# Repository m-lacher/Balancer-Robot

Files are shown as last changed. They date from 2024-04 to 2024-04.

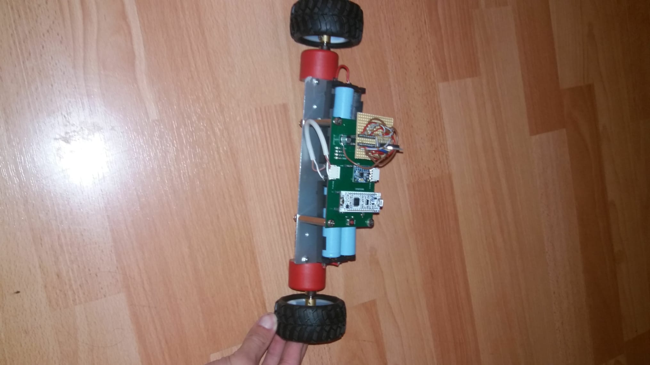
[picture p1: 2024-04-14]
Documentation/Bilder/b0cf12ee-8584-46d6-8bd2-6b98735de912.jpg

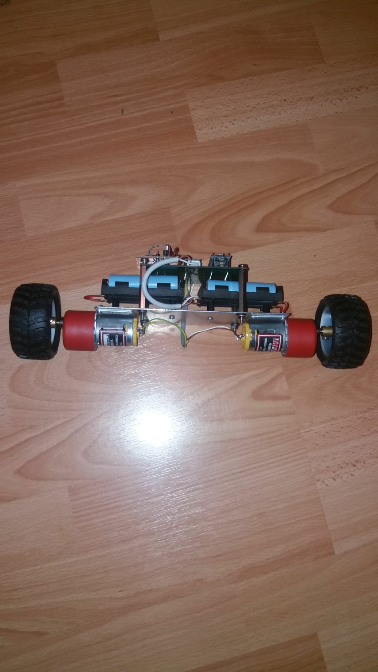
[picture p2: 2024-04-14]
Documentation/Bilder/f380182b-9d1d-40e0-8857-80b62b0fd65c.jpg

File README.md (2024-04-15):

# Balancer-Robot
## Introduction
The Balancer Robot was my project for the "Berufsmaturitätsarbeit" (BMA). The goal of this project was to design a self-balancing two wheeled robot. 
## Note
The project was quite a bit of a challenge, as I hadn't had much knowledge about control systems or desinging the mechanical system. However after many tries, the robot balanced itself quite good. This can be seen in the [BalancerRobot.mp4](/Balancer%20Robot.mp4) video.

## Further documentation
Further information can be found in the [Documentation](/Documentation/) folder.\
Project documentation: [BMA-BalancerRobot.pdf](/Documentation/BMA-BalancerRobot.pdf)

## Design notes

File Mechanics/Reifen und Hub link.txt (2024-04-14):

Reifen:	https://www.play-zone.ch/de/wheel-72x34mm-blau.html

Hub:	https://www.play-zone.ch/de/wheel-hub.html

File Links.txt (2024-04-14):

batterie holder:	https://www.digikey.ch/product-detail/de/keystone-electronics/1047/36-1047-ND/5057794?productid=5057794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

i2c problem:		https://os.mbed.com/questions/84778/I2C-doesn-t-work-on-F303K8/
			https://www.mikrocontroller.net/topic/454653

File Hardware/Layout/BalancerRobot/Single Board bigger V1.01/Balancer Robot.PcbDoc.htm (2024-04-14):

Reporting Options

# File in Previous Format

Date | : | 22.03.2023
Time | : | 16:07:12
Filename | : | C:\Backup HDD\BalancerRobot\Hardware\Layout\BalancerRobot\Single Board bigger V1.01\Balancer Robot.PcbDoc

Version | Warning

This file was generated by an earlier version of the software

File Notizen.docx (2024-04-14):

15.09.2019: PWM programmiert, erster Versuch

17.09.2019: Ansteuerung Sensor erfolgreich.

19.09.2019: Layout bestellt.

19.09.2019: Testversuche mit Sensor

23.09.2019: Weitere Testversuche, Auswertung.

30.09.2019: Mechanische Grundplatte bei Andreas in Auftrag gegeben.

03.10.2019: Erste Version zusammengebaut.

04.10.2019: Bemerkt, dass Pullup Widerstände fehlen. Neuer Sensor bestellt

08.10.2019: Diskussion mit Volker über die physikalischen Kräfte sowie eine Reglung durch Impulsansteuerung der Motoren. (Pendelprinzip)

15.10.2019: Problem mit Umzug (Mechanische und elektronische Fertig erschwert)

17.10.2019: Problem mit I2C festgestellt.

21.10.2019: Mikrocontroller ausgelötet wegen Widerstandsbrücken, am Abend festgestellt, dass Mikrocontroller kaputt ist.

22.10.2019: Mikrocontroller ausgelötet, Leiterplatte kaputt. Neue Bauteile bestellt.

23.10.2019: An Doku gearbeitet, am Nachmittag im Geschäft um neue Leiterplatte zu bestücken, Motoren getest, festgestellt dass IC zu heiss. IC getauscht, Kurzschluss, Mikrocontroller und IC kaputt.

24.10.2019: Software überarbeitet, test ohne Motoren gelungen, Nachmittag neue Motor Treiber in Nänikon abgeholt.

25.10.2019: Neuer Motortreiber auf Adapterplatte gelötet, Ansteuerung funktionierte, später dann jedoch bei einem Motor nicht Rückwärts.

28.10.2019: Viel an der Dokumentation gearbeitet.

30.10.2019: Festgestellt, dass ein Wackelkontakt bei der Adapterplatine vorhanden ist, weshalb der Motor nicht drehte.

31.10.2019: Entschieden ein neues Layout zu erstellen.

04.11.2019: Layout angepasst

05.11.2019: Layout online bestellt.

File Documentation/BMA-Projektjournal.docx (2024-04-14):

Lacher Markus, BEL16a

markuslacher@hotmail.ch

Balancer Robot

Prozessdokumentation

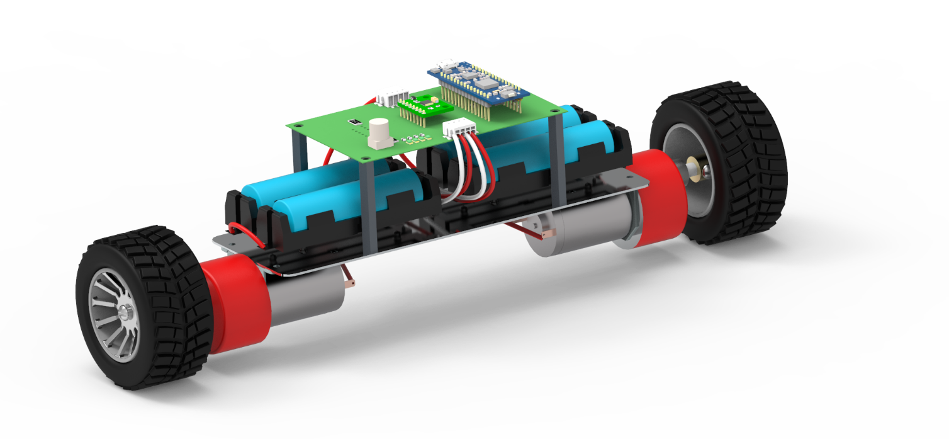
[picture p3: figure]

Berufsmaturitätsschule Zürich

Technik, Architektur, Life Sciences

Betreuer: H.P. Lutz

Abgabe: 26.11.2019

# Projektvereinbarung

## Thema

Der Balancer Robot soll ein Fahrzeug werden, welches sich selbst ausbalanciert. Es soll auf 2 Rädern vor- und zurückfahren, um nicht umzufallen. Ein grosser Teil des Projekts umfasst das Entwickeln der Elektronik und der Software des Fahrzeugs. Mithilfe eines Beschleunigungs- und Gyrosensors soll die Neigung des Fahrzeugs bestimmt werden können. Die Software soll dann per Regelungsalgorithmus die Motoren ansteuern, damit der Balancer Robot vor dem Umfallen bewahrt wird. Sowohl die Elektronik, als auch die Software bilden eine Herausforderung, der ich mich jedoch gewachsen fühle. Der Regelungsalgorithmus wird wahrscheinlich die grösste Herausforderung werden. Fokus der Arbeit ist also das Bereitstellen eines funktionstüchtigen und optimierten Prototyps. Sollte dieser funktionieren, werde ich mit ersten Selbstversuchen simpler Regelungsalgorithmen beginnen.

## Eigene Fragestellung / Untersuchungsgegenstand

### Leitfrage

Ist es möglich, mithilfe eines Beschleunigungs- und Gyrosensors und zwei DC-Motoren ein Fahrzeug auf 2 Rädern auszubalancieren? Untersucht werden soll dabei einerseits die Physik hinter dem Ausbalancieren, andererseits soll eine Elektronik entwickelt werden, die bestmöglich auf das Ausbalancieren optimiert ist. Zusätzlich möchte ich Gedanken und Recherche über Regelungsalgorithmen ausführen, um allfällig selber den Regelungsalgorithmus für das Ausbalancieren schreiben zu können.

### Hypothese

Ich denke, das Bestimmen der Neigung mithilfe des Beschleunigungs- und Gyrosensors sollte möglich sein. Auch das Entwickeln der Elektronik traue ich mir zu. Schwieriger wird es bei der Software für den Mikrocontroller. Die ist vermutlich relativ komplex. Aber da ich aktuell im Geschäft über programmieren von Embedded Software geschult werde, möchte ich mich dieser Herausforderung stellen. Die grösste Schwierigkeit sehe ich im Regelungsalgorithmus, da ich mich bis anhin weder in der Schule noch im Geschäft mit Regelungstechnik befasst habe.

### Methoden und Vorgehen

Geplant sind 4 Projektmeilensteine: Zu Beginn das Analysieren des physikalischen Grundprinzips. Danach soll die Elektronik und die Mechanik für den ersten Prototypen entwickelt werden. Im dritten Schritt soll Software entwickelt werden, um die Elektronik anzusteuern. Der vierte Meilenstein wird das Entwickeln eines Regelungsalgorithmus sein.

## Hilfsmittel

Messgeräte für das Testen der Elektronik, sowie Debugger für die Software. 3D-CAD Programm für die Mechanik.

## Kontaktpersonen, Informationsstellen, Institutionen

Eine wichtige Kontaktperson wird Herr Lutz sein, weil ich sicherlich Unterstützung beim Analysieren des physikalischen Prinzips brauche. Herr Malacarne, mein Elektrotechniklehrer aus der Berufsschule, wird meine erste Anlaufstelle sein, wenn es Probleme in der Elektronik gibt. Für den Regelungsalgorithmus könnte ich einen Projektleiter aus meinem Geschäft ansprechen, Herrn Gwerder, da dieser einen Master in Regelungstechnik besitzt.

## Persönlicher Bezug / Motivation

Das Projekt ist eine grosse Herausforderung für mich. Es wird viel Zeit in Anspruch nehmen und es ist gut möglich, dass am Ende das Ausbalancieren nicht funktioniert. Dennoch bin ich motiviert, mein Können unter Beweis zu stellen und das Beste aus dem Projekt zu machen. Ich wollte mich schon seit Längerem mit Regelungstechnik auseinandersetzen, hatte bisher aber nicht die Zeit dafür. Dieses Projekt kombiniert ideal meine Interessen im Bereich der Softwareprogrammierung, Entwicklung von Elektronik und Physik.

# Zeitplan

# Protokoll der Zwischenbesprechung

Eine offizielle Zwischenbesprechung wurde nicht durchgeführt. In der Projektwoche setzte sich Herr Lutz kurz zu mir und fragte mich nach dem Stand und den Problemen des Projekts. Er gab mir Tipps und Vorschläge und überprüfte, ob ich mich auf dem richtigen Weg befinde. Ein Protokoll wurde nicht geführt.

# Projektjournal

Datum | Ausgeführte Arbeiten | Aufwand
19.08.2019 | Erste Überlegungen zum Projekt und zu den physikalischen Kräften gemacht. | 3h
23.08.2019 | Informiert über Gyrosensoren und Beschleunigungssensoren. Sensorboard bestellt. Zwei verschiedene Motoren auf Conrad bestellt. | 2h 0.5h 0.5h
27.08.2019 | Mechanische Planung, Grobkonzept des ersten Prototyps erstellt. Mindestanforderung für das Motorendrehmoment bestimmt. | 1.5h 1h
28.08.2019 | Festgestellt, dass die bestellten Motoren ein zu kleines Drehmoment aufweisen. Motor mit mechanischer Übersetzung auf Conrad bestellt. | 1.5h
15.09.2019 | Erste Software geschrieben, um die PWM Ansteuerung des Mikrocontrollers zu testen. | 1.5h
17.09.2019 | Ansteuerung des Sensors MPU-6050 erfolgreich getestet. Schema für die Leiterplatte entwickelt. | 2h 1h
19.09.2019 | Erste Leiterplatte gelayoutet und bestellt. | 8h
23.09.2019 | Weitere Testversuche mit dem Sensor, Softwaremodul programmiert. | 2h
25.09.2019 | Python-Skript programmiert, um die Sensorwerte mit dem Computer auslesen zu können. | 1.5h
30.09.2019 | Mechanische Grundplatte gezeichnet und einem Mechaniker im Betrieb in Auftrag gegeben. | 1h
02.10.2019 | Leiterplatte bestückt. | 1.5h
03.10.2019 | Erster Prototyp zusammengebaut. | 1h
04.10.2019 | Die Ansteuerung des Sensors funktionierte nicht mehr auf der Leiterplatte. Dafür funktionierte die erste Ansteuerung der Motoren. | 0.5h 1h
06.10.2019 | Weitere Softwaremodule fertiggestellt. (GPIO-Treiber, LED-Treiber, ADC-Treiber) | 6h
08.10.2019 | Ich habe spontan im Betrieb eine Stunde lang mit einem Physiker über die physikalischen Kräfte des Balancer Robots diskutiert. Er hat mich auf das Pendelprinzip aufmerksam gemacht. | 1h
14.10.2019 | Weitere Softwareteile programmiert. | 8h
15.10.2019 | Die nächsten beiden Wochen zügelt mein Betrieb den Standort. Dadurch ist das Testen und Anpassen der Elektronik sowie Mechanik erschwert für mich. Ich nahm diverse Werkzeuge mit nach Hause, damit ich für den Notfall auch Zuhause ein bisschen „basteln“ kann. | -
17.10.2019 | Heute habe ich endlich herausgefunden, weshalb die Ansteuerung des Sensors auf der Leiterplatte nicht mehr funktioniert. Das verwendete Mikrocontrollerboard hat zwei Lötbrücken, welche jeweils zwei Pins des Mikrocontrollers miteinander verbindet, damit das Mikrocontrollerboard mit dem Arduino UNO kompatibel ist. Dadurch war ein PWM Pin für den Motor mit der Datenleitung der I2C Schnittstelle verbunden. Somit konnte der Mikrocontroller nicht mehr mit dem Sensor kommunizieren. | 2.5h
21.10.2019 | Das Mikrocontrollerboard musste von der Leiterplatte ausgelötet werden, damit ich die Lötbrücken auf der Unterseite des Boards auftrennen konnte. Danach testete ich die Software, um zu sehen ob die Motoren anhand der Sensorwerte angesteuert werden. Ich musste feststellen, dass ich noch diverse Fehler in der Software hatte, welche ich dann überarbeitete. Am Abend wollte ich die Erweiterung der Software testen, musste aber feststellen dass der Mikrocontroller defekt war. | 3.5h
22.10.2019 | Beginn der Projektwoche
22.10.2019 | Im Labor der BMS habe ich den Mikrocontroller ein zweites Mal ausgelötet, um diesen zu ersetzen. Dieser Prozess war beim ersten Mal schon aufwändig. Durch die mechanische Belastung beim Auslöten ist die Leiterplatte kaputt gegangen. An der Software gearbeitet, Taster-Ansteuerung umgesetzt. Dokumentation erweitert. | 2h 2.5h 1h
23.10.2019 | Am Morgen an der Dokumentation gearbeitet. Am Nachmittag ins Geschäft gefahren, neue Leiterplatte bestückt. Zuhause habe ich weitere Softwaretests durchgeführt und musste feststellen, dass ein Motor nicht korrekt angesteuert wird und dass der Motortreiber im Betrieb sehr heiss wird. Ich vermutete dass der Motortreiber kaputt ist und ersetzte ihn. Direkt beim Einschalten des Balancer Robots funkte es und der ersetzte Motortreiber war beschädigt. | 4.5h 2h 2h

24.10.2019

Am Morgen arbeitete ich weiter an der Software. Die Ansteuerung der Motoren anhand der Sensormesswerte funktionierte, jedoch ohne den Motortreiber. Ich mass einfach das PWM-Ausgangssignal des Mikrocontrollers.

Zusätzlich suchte ich nach einem neuen Motortreiber mit mehr Leistung. Da ich unter Zeitdruck stehe, rief ich direkt beim Lieferant an und bestellte den neuen Typ.

Im Verlaufe des Nachmittags fuhr ich nach Nänikon und holte den bestellten Motortreiber direkt beim Lieferanten ab, um zwei Tage Lieferzeit zu sparen.

Danach fuhr ich ins Geschäft und begann eine Adapterplatine zu bauen, damit ich den neuen Motortreiber auf den alten Sockel stecken kann.

3h

1.5h

1h

3h
25.10.2019 | Da ich gestern bis spät abends im Geschäft war, jedoch nicht fertig wurde mit der Adapterplatine, fuhr ich erneut ins Geschäft und bestückte die Adapterplatine fertig. Am Mittag fuhr ich nach Zürich für das gemeinsame Mittagessen. Am Nachmittag waren die Präsentationen der einzelnen Gruppen. | 3h -
25.10.2019 | Ende der Projektwoche
28.10.2019 | Arbeit an der Dokumentation | 3.5h
30.10.2019 | Ich musste feststellen, dass die Adapterplatine einen Wackelkontakt aufweist. Dadurch konnte ich einen Motor nicht richtig ansteuern, weshalb ich nicht wie geplant an der Regelungssoftware arbeiten konnte. | 1.5h
31.10.2019 | Ich entschied mich, dass die Adapterplatine eine zu grosse Bastelei ist. Ich begann das Layout anzupassen, damit die Elektronik fehlerfrei funktioniert. | 2h
05.11.2019 | Ich habe die Anpassung des Layouts fertiggestellt und die neue Leiterplatte direkt bestellt. | 2.5h
11.11.2019 | Die neue Leiterplatte ist angekommen. | -
12.11.2019 | Ich habe die neue Leiterplatte bestückt. | 1.5h
14.11.2019 | Endlich konnte ich mit den ersten Versuchen der Regelungselektronik anfangen. Leider musste ich feststellen, dass ich die Messwerte noch optimieren muss, da das Aufrichten des Fahrzeugs die Messwerte des Beschleunigungssensors beeinflusst, was ich bisher noch nicht bedacht hatte. | 2h
15.11.2019 | P-Regler getestet, ohne Erfolg | 2h
16.11.2019 | Dokumentation | 3h
17.11.2019 | Dokumentation | 4.5h
19.11.2019 | Projektjournal | 2h
20.11.2019 | Dokumentation | 1.5h
21.11.2019 | Dokumentation | 1.5h
22.11.2019 | Hauptteil fertiggestellt, Reflexion | 4h
23.11.2019 | Total | 105.5h

# Reflexion

Das Projekt war eine grosse Herausforderung für mich. Mir war von Beginn an klar, dass ich an meine Grenzen des Könnens stossen werde. Denn das Projekt verlangt nach sehr viel Wissen über Softwareprogrammierung, Entwicklung von Hardware und auch physikalisches Verständnis. Doch genau dies war für mich persönlich ein starker Anreiz, denn ich wollte mein Können unter Beweis stellen.

## Einzelarbeit

Ich durfte das Projekt als Einzelarbeit durchführen. Dies ersparte mir viel organisatorischen Aufwand, da ich die Arbeit nicht aufteilen musste. Da ich im Geschäft keine Lernenden in meiner Stufe habe und auch sehr weit weg von meinen Klassenkameraden wohne, konnte ich mir durch die Einzelarbeit viel Arbeitsweg sparen.

## Zeitplanung

Da ich mich erst in den Sommerferien für dieses Projekt entschieden habe und auch auf das Okay vom Betreuer bis nach den Sommerferien warten musste, war die Zeit sehr knapp. Deshalb plante ich den Zeitplan sportlich, was bei technischen Projekten immer suboptimal ist, denn man sollte stets Raum für Fehler und unerwartete Probleme einplanen. Ich setzte mir also zum Ziel, den ersten lauffähigen Prototypen in den Herbstferien fertigzustellen. Dafür waren in den Wochen bis und mit den Herbstferien über 30 Stunden Arbeitszeit eingeplant. Diese Schätzung war ziemlich gut, ich hatte tatsächlich in den Herbstferien alle Bestandteile für den ersten Prototyp bereit.

In der Projektwoche wollte ich die Software fertig schreiben und bereits mit ersten allfälligen Optimierungen des Prototyps starten. Ich war dem Zeitplan somit voraus. Doch in der Projektwoche musste ich dann feststellen, dass die Ansteuerung der Motoren durch den gewählten Motortreiber nicht korrekt funktionierte. Dies war ein Schock für mich, denn ich hatte diesen getestet, bevor ich mit der Entwicklung der Leiterplatte begonnen hatte. Denn nun musste ich einen Ersatz suchen, was aufgrund der Lieferzeiten und der Integrierung auf die bestehende Hardware sehr zeitintensiv war. Schlussendlich musste eine neue Leiterplatte entwickelt werden, welche 3 Wochen vor dem Abgabetermin geliefert wurde. Diese musste dann noch bestückt und eingebaut werden. Mir blieben also nur noch 2 Wochen Zeit, um Versuche mit verschiedenen Regelungsalgorithmen durchzuführen.

Dies ärgerte mich, da ich gerne mehr Zeit in die Versuche investiert hätte. Und es wäre auch schön gewesen, hätte ich es tatsächlich geschafft, das Fahrzeug auszubalancieren. Trotzdem bin ich zufrieden mit der Zeitplanung, denn sie war relativ präzise. Dies verdanke ich hauptsächlich dem Training durch die Berufsschule, in welcher wir bereits 2 technische Projekte über ein ganzes Semester lang mit Zeit- und Budgetplanung durchgeführt haben.

## Analysieren der Hypothese

Auch das Analysieren der Hypothese war zufriedenstellend. Ich konnte durch interessante Messversuche und Experimente aufzeigen, wie der Winkel des Fahrzeugs bestimmt werden kann. Auch das Ansteuern der Motoren konnte ich gut umsetzten, sowie auftretende Fehler korrigieren. Ich bin sehr zufrieden mit den Grafiken und Erklärungen in der Produktdokumentation.

## Optimierungsvorschläge

Ein wichtiger Verbesserungsvorschlag sehe ich in der Zielsetzung. Das Projekt war interessant und herausfordernd, jedoch steckte ich meine Ziele etwas gar hoch. Denn das Entwickeln des Prototyps war bereits sehr anspruchsvoll, das Programmieren und Anwenden eines Regelungsalgorithmus war schlussendlich einfach zu viel. Für eine nächste Arbeit würde ich ein kleineres Ziel stecken, dieses dann dafür bestmöglich umsetzen.

Auch der Arbeitsaufwand für das Produkt war meiner Meinung nach zu hoch. Ich war so ambitioniert darin, das Fahrzeug zum Laufen zu bringen, dass ich die Dokumentation sehr lange vernachlässigt habe. In den letzten beiden Wochen vor Abgabe musste ich dann sehr viel Zeit in die Dokumentation investieren. Schlussendlich bin ich zufrieden mit der Produktdokumentation, aber ich behaupte, dass die Qualität der Arbeit unter dem Zeitdruck doch etwas gelitten hat.

## Fortsetzung

Das Projekt ist noch nicht abgeschlossen, denn es läuft in der Berufsschule weiter. Dort habe ich nun bis Semesterende Zeit den Prototypen zu optimieren und an einem funktionierenden Regelungsalgorithmus zu arbeiten. Dies freut mich, denn ich möchte das Ausbalancieren unbedingt auch noch hinkriegen.

M.Lacher Seite 10 von 10

Balancer Robot

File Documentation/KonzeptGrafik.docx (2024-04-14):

PWM

Aufbereitete Daten

Stellgrösse

Sensordaten

L293D

Motor Treiber

Regler

Daten Verarbeiter

Interrupt

Kommunikation

MPU6050

MPU6050 Treiber

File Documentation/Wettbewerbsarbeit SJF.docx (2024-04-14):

Lacher, Markus

markuslacher@hotmail.ch

28.10.2018

Wichtig

Dieses Projekt ist ihm Rahmen der Berufsmaturitätsarbeit 2019 an der BMZ entstanden. Da der Abgabetermin für diese Arbeit erst am 26.11.2019 ist und auch die Information über die Stiftung Schweizer Jungend Forscht erst am 22.10.2019 an der Schule kommuniziert wurde, ist meine Arbeit noch nicht fertig.

Trotzdem möchte ich diese Arbeit gerne Einreichen, damit Sie sich ein Bild über das Projekt machen können und mir vielleicht sogar eine Teilnahme ermöglichen.

Besten Dank!

Balancer Robot

Berufsmaturitätsarbeit

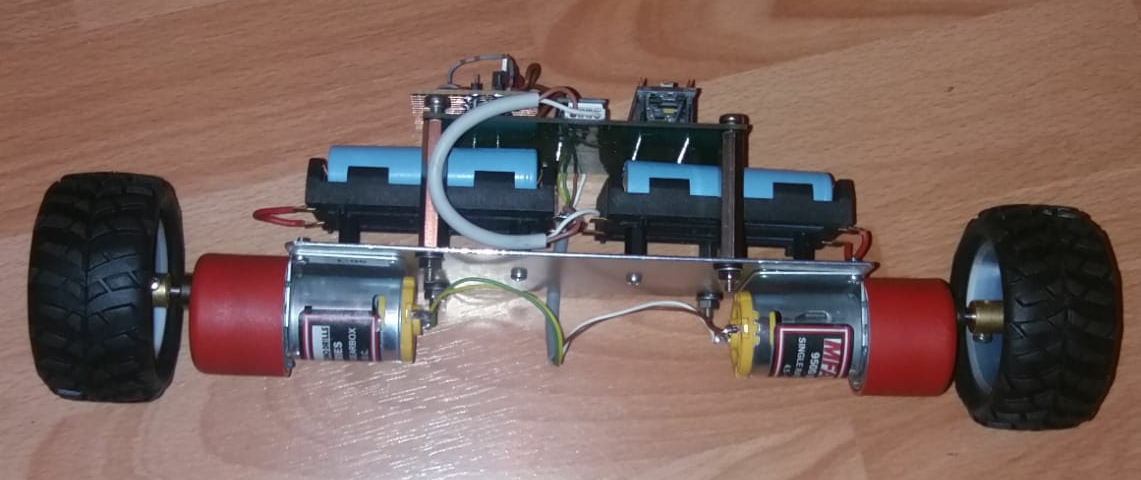
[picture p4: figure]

Abstract

# Einleitung

## Fragestellung

# Hauptteil

## Konzept

Der Balancer Robot ist im Prinzip nichts anderes als eine Regelungselektronik. Über Sensorik wird eine physikalische Grösse gemessen und mithilfe der Regelung wird ein Aktor angesteuert, sodass sich ein gewollter Sollwert einstellt.

Der Balancer Robot misst mithilfe eines 3-Achsen Gyrosensors und eines 3-Achsen Beschleunigungssensors die Kräfte die auf den Roboter wirken. Diese Messwerte werden von einem Mikrocontroller eingelesen. Dieser verarbeitet die Messwerte und Steuert die Motoren des Roboters an, um diesen vom Umfallen zu bewahren.

### Physikalisches Grundprinzip

Kräfte beschreiben, evtl. Pendelprinzip

### Software

MPU6050 Treiber

Daten Verarbeiter

Regler

Motor Treiber

L293D

MPU6050

Interrupt

Kommunikation

Sensordaten

Aufbereitete Daten

Stellgrösse

PWM

Blau: Sensoren

Grün: Mikrocontroller (Software)

Rot: Aktoren

Der MPU6050-Treiber konfiguriert den Sensor, sodass dieser mit einer Frequenz von 100Hz die 3-Achsen des Gyrosensores, sowie die 3-Achsen des Accelerometers misst. Über einen Interrupt Pin wird dem Mikrocontroller signalisiert, dass die Daten bereitstehen. Der Mikrocontroller liest dann sofort die Daten aus.

Die Sensordaten werden dem Datenverarbeiter übergeben. Dieser berechnet den dynamischen Mittelwert der Daten, um diese zu Glätten und Störungen herauszufiltern.

Die Aufbereiteten Daten werden dem Regler übergeben. Dieser errechnet mithilfe des Regelalgorithmus die Stellgrösse für die Motoren.

Die Stellgrösse wird dem Motortreiber übergeben. Aufgrund der Stellgrösse steuert der Motor Treiber die Motoren per PWM Signal an.

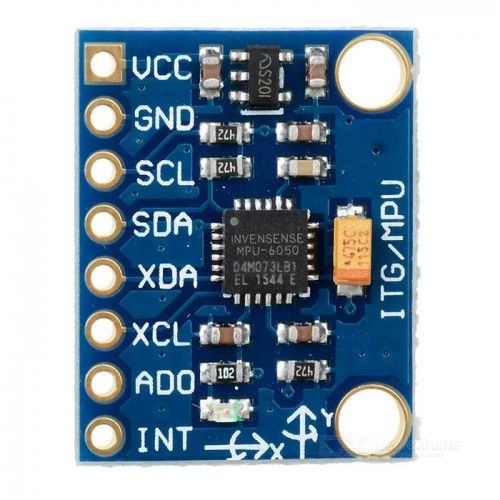
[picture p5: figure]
Bildergebnis für mpu6050

## Sensorik

Die rechts abgebildete Sensorleiterplatte ist mit dem MPU-6050, ein sehr verbreiteter Gyro- und Beschleunigungssensor, bestückt. Dieser misst in allen 3-Achsen die Beschleunigung, sowie die Rotationsgeschwindigkeit. Über die digitale I2C Kommunikationsschnittstelle kann der Sensor konfiguriert und ausgelesen werden.

### Rotation

Der Gyrosensor misst die Rotation um eine Achse in Grad/s. Je nach Konfiguration kann der Sensor bis zu 1000°/s messen. Befindet sich der Sensor in Ruhelage, ist die Rotation aller Achsen gleich 0. Man könnte den Winkel bestimmen indem man die Rotationsgeschwindigkeit pro Zeiteinheit aufsummiert, jedoch driftet die Berechnung des Winkels ab, da Messfehler addiert werden und somit das Ergebnis mehr und mehr verfälscht wird.

Y

X

Z

### Beschleunigung

Die Beschleunigung wird in m/s² gemessen. Je nach Konfiguration kann der Sensor bis zu +/- 16G messen, dass entspricht der 16-fachen Erdbeschleunigung also ca. 160m/s².

Liegt der Sensor still, ist die einzige Kraft, welche auf ihn wirkt, die Erdbeschleunigung. Würde der Sensor flach auf dem Tisch liegen wie oben abgebildet, dann misst man auf der Z-Achse eine Beschleunigungskraft von 9.81m/s². Auf der X- und Y-Achse liegt keine Kraft an. Beginnt man nun den Sensor zu kippen, teilt sich die Kraft der Erdbeschleunigung auf die Achsen auf. Mithilfe von Vektorgeometrie lässt sich dann der Winkel bestimmen.

g

X

Z

∝ =arctan(Z/X)

Um den Roboter auszubalancieren versucht die Regelung den Winkel Alpha immer bei 90° zu halten.

Z

g

X

α

### Konfiguration

Der Sensor wird so konfiguriert, dass er mit einer Frequenz von 1000Hz die Messwerte der 6-Achsen aufzeichnet. Sobald diese bereit zum Auslesen sind, wird dies über den Pin INT (Interrupt) signalisiert. Die Messwerte werden dann sofort vom Mikrocontroller ausgelesen und verarbeitet.

### Datenverarbeitung

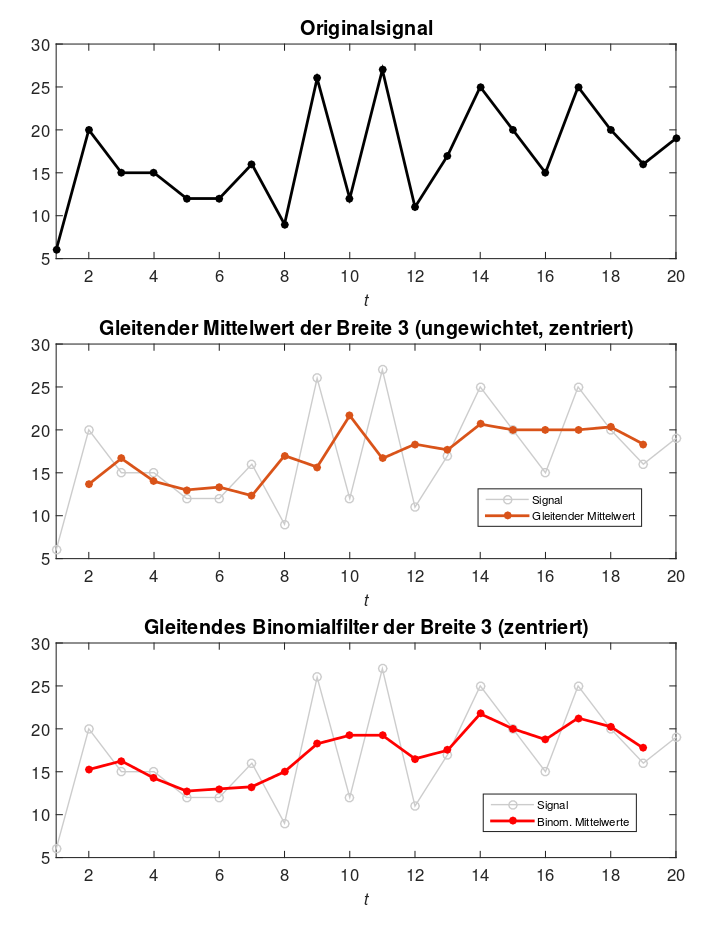
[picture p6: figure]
Bildergebnis für gleitender mittelwert
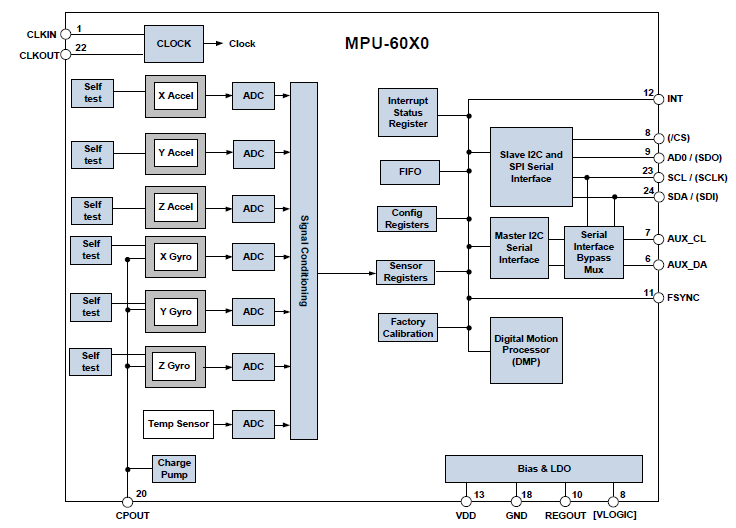
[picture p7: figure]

Der Sensor besitzt einen internen DMP. Richtig konfiguriert filtert dieser die Messdaten mit einem Tiefpassfilter, damit Störungen bereits intern im Sensor herausgefiltert werden können.

Abbildung 1: (Wikipedia, 2019)

Abbildung 2: (InvenSense, 2019)

Auch per Software werden die Daten nochmals optimiert. Das Daten Verarbeiter Modul glättet die Messwerte mithilfe eines gleitenden Mittelwerts.

Durch das Tiefpassfilter und den gleitenden Mittelwert werden Störungen, Messfehler und Rauschen des Sensor minimiert.

Einziger Nachteil: Durch das Verarbeiten der Daten wird die Zeitverzögerung der tatsächlichen Messung bis zu deren Verarbeitung durch Regler grösser. Dies kann das Verhalten des Reglers negativ beinflussen.

### Sensor Auswertung

Um den Sensor zu testen wurde eine erste Testsoftware für den Mikrocontroller geschrieben, welche die gemessen Werte über die UART-Schnittstelle des Mikrocontrollerboards an einen angeschlossenen PC sendet. Zusätzlich wurde eine Python Software entwickelt, welche die gesendeten Daten verarbeitet und diese in eine Excel Tabelle schreibt. Dadurch konnte das Verhalten des Sensors analysiert werden.

Abbildung 3: Messung des Acceleromters

#### Kippen von Hand

Der Sensor wurde von Hand um alle drei Achsen gedreht. Die Messwerte sind stark verrauscht, da einerseits die Handbewegungen nicht exakt sind, zudem ist das digitale Tiefpassfilter des Sensors nicht eingeschaltet.

Die Y-Achse entspricht der Kraft in G und die X-Achse der Nummer des Messwerts.

Abbildung 4: Messung mit gleitendem Mittelwert

#### Gleitender Mittelwert

Im Excel wurde der gleitende Mittelwert aus den letzten 5 Werten gebildet. Das Rauschen wurde gedämpft und Störungen bzw. Spitzen wurde geglättet.

Grafiken des Gyrosensors anfügen

## Elektronik

### Ansteuerung Motor

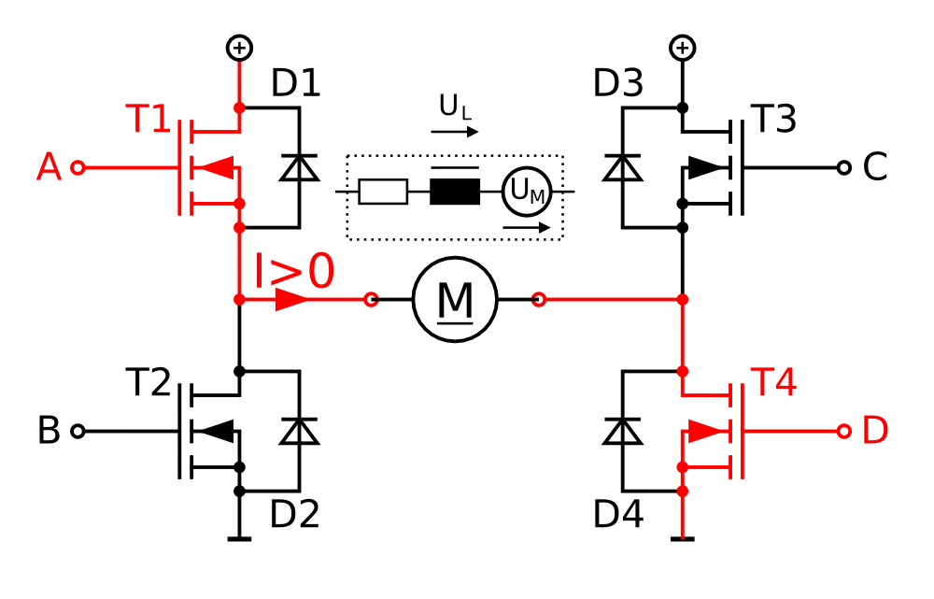
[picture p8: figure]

Ein DC-Motor besitzt zwei Anschlüsse. Ändert die Richtung des Stromes, wechselt auch die Drehrichtung des Motors. Um dieses Wechseln des Stromes elektronisch umzusetzen wurde eine H-Brücke, auch Vierquadrantensteller genannt, verwendet.

Abbildung 5: (Wikipedia, 2019)

Prinzip: Die Schaltung besitzt eine Motorspannung U+ und einen GND. Schaltet der Transistor T1 und T4 während T2 und T3 sperren, dann liegt vom linken zum rechten Anschluss des Motors eine positive Spannung an.

Sperrt T1 und T4 und leiten dafür T2 und T3, dann liegt eine negative Spannung vom linken zum rechten Anschluss an. Die Drehrichtung ändert.

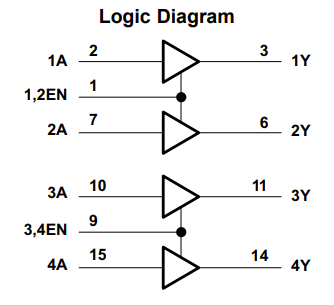
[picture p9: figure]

Da ich die Anschlüsse A-D der H-Brücke mit CMOS-Logik (0 – 3.3V, gegeben durch Mikrocontroller) ansteuern möchte, die Motorspannung U+ jedoch bis zu 16V beträgt, müsste für den Anschluss A und C noch zusätzliche Komponenten für die Spannungstransformation verwendet werden. Ausserdem bräuchten die Bauteile einzeln verbaut mehr Platz. Deswegen wird der IC L293D verwendet.

Abbildung 6: (Texas Instruments, 2019)

Der Baustein besitzt 4 High-Voltage Treiber. Über den Eingang A kann mit 0V oder 3.3V der Ausgang Y auf 0V oder auf den Level der Speisespannung geschaltet werden. Die Speisespannung kann bis zu 36V betragen. So kann an 1Y und 2Y der erste Motor und über 3Y und 4Y der zweite Motor angeschlossen werden.

Die Ausgänge können bis zu 1.2A liefern und auch „schlucken“. Mit den beiden Signalen 1,2EN und 3,4EN können die Treiber aktiviert werden.

Die Software soll die Leistungsabgabe des Motors steuern können, ansonsten ist eine Regelung nicht möglich. Um diese Steuerung zu erreichen wird die H-Brücke mit einem PWM Signal angesteuert. PWM steht für Pulse Wide Modulation.

Die Spannung über dem Motor soll reguliert werden. Da die Hardware jedoch nur zwei Zustände einstellen kann, (siehe H-Brücke) wird mit ständigem Ein- und Ausschalten die Spannung über dem Motor reguliert.

Abbildung 7: (Mikrocontroller.net, 2019)

T= t_(ein) + t_(aus)

f= 1/T

Tastgrad= (t_(ein))/T

### Motor Stromaufnahme

#### Problem

Die ersten Tests mit dem L293D mit PWM Ansteuerung verliefen gut. Die Motoren liessen sich in beide Richtungen drehen. Der L293D wurde aber relativ heiss. Doch als ich den Roboter das erste Mal zusammengebaut hatte und diverse Probleme nach einer Zeitintensiven Fehlersuche endlich beheben konnte, wollte ich die komplette Software mit einem einfachen Regelungsalgorithmus testen.

Der L293D Baustein wurde noch heisser als sonst und ein Motor arbeitete nicht richtig. Ich vermutete der Baustein sei beschädigt, da ich in Anfangs falsch angeschlossen hatte. Als ich den Baustein austauschte in der Hoffnung die Ansteuerung der Motoren würde funktionieren, ging dieser direkt bei Einschalten der Motoren kaputt, der Mikrocontroller funktionierte auch nicht mehr.

#### Theorie

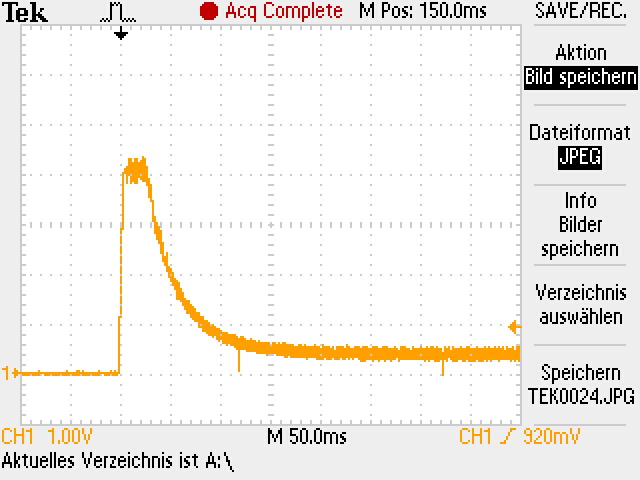
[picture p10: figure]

Im Projekt werden Gleichstrom- Bürstenmotoren eingesetzt. Diese erzeugen durch die Rotation der Achse eine Gegeninduktion in der Spule, welche den Strom ausbremst. Je höher die Drehzahl des Motors, desto grösser ist die Gegenspannung und dementsprechend wird der Strom umso kleiner. Dies ist auch der Grund für die Tatsache, dass das Drehmoment bei Elektromotoren bei steigenden Drehzahlen abnimmt.

Parameter:

U0: 15V

RMess 2Ω

RMotor 3Ω

Abbildung 8: Messaufbau

Abbildung 9: Messung 1, Start des Motors

##### Analyse

Um das Problem zu analysieren wurde ein Messversuch durchgeführt. Über einen 2 Ohm Messwiderstand wurde mithilfe eines Oszilloskops die Stromaufnahme des Motors aufgezeichnet. Dieser ist nicht ideal, da der Ohm’sche Widerstand der Motorspule 3Ohm beträgt. Dies führt bei grossen Strömen zu Verminderung der Spulenspannung über dem Motor, da über dem Messwidertand eine zu grosse Spannung abfällt.

Trotzdem war der Fehler bereits nach der ersten Messung offensichtlich. Im Stillstand induziert die Motorwelle in der Spule noch keine Gegenspannung. Beim Einschalten wirkt somit ganz kurz die Impedanz der Spule, danach nur noch der Ohm’sche Widerstand von 3Ω. Bei 15V entsteht dann über einen Zeitbereich von 40ms ein Strom von über 4 Ampere. Danach sinkt der Strom innerhalb von 60ms auf 200mA. Dies entspricht ziemlich genau den Angaben des Datenblatts, welches bei keiner mechanischen Belastung einen Strom von 180mA angibt.

Der Motortreiber L293D kann pro Ausgang einen konstanten Strom von 1.2A Ampère liefern, was für den Normalbetrieb des Motors ausreichen würde. Doch der kurzzeitige Stromspitz beim Anfahren genügt um den Motortreiber zu zerstören.

Um der hohen Stromanforderung gerecht zu werden, wurde ein neues IC getestet. Der L298 ist ähnlich Aufgebaut wie der alte Treiber L293D, jedoch kann dieser einen Strom von 2A Liefern und kurzzeitige Spitzen bis zu 3A Ampere. Dieser wird im Betrieb auch sehr warm, funktioniert jedoch.

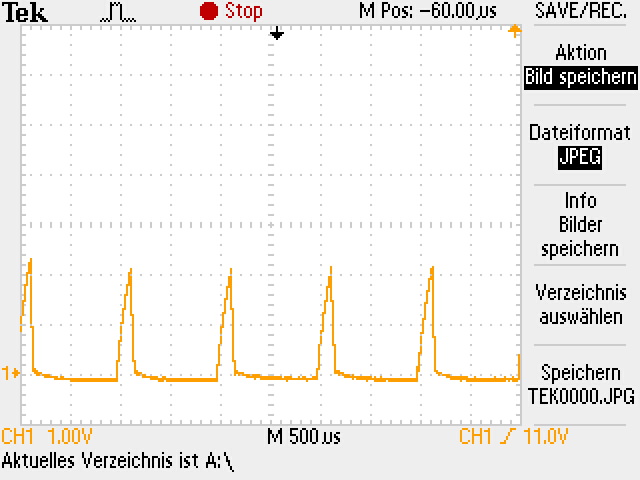
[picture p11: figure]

Strommessung bei Anfahren mithilfe von PWM. Man sieht die PWM Frequenz von 1kHz sowie das Stromverhalten eines LC Gliedes, da die Kurve einer e-Funktion ähnelt. Da die Spannung nur kurzeitig eingeschaltet ist, steigt der Strom nicht über 1.5A, weshalb der L293D intakt bleibt.

Abbildung 10: Messung des Stroms bei Anfahren mit PWM

Gefährlich wird es, wenn der Motor mit einem hohen PWM Wert anfährt.

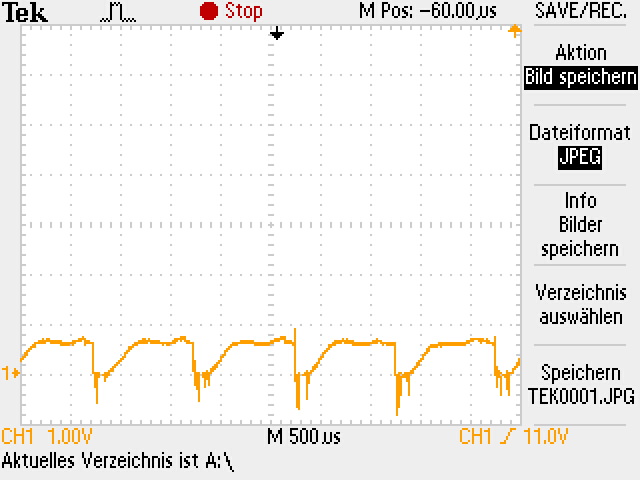
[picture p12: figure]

Abbildung 11: Messung des Stroms bei PWM 60%

Messung des Stroms bei laufendem Motor mit einem PWM von 60%. Man sieht gut, dass der Motor im Betrieb weniger Leistung benötigt als beim Anfahren. In der Messung sieht man auch gut wie der PWM arbeitet. Die negativen Stromspitzen werden beim Abschalten der Spule durch deren Selbstinduktion erzeugt.

## Mechanik

Die Mechanik spielt eine entscheidende Rolle im Projekt, um den Erfolg zu garantieren. Der Roboter sollte möglichst leicht sein, damit das benötigte Drehmoment um den Roboter wieder aufzurichten möglichst klein bleibt. Ausserdem muss auf die Gewichtsverteilung geachtet werden, um den Schwerpunkt tief zu halten.

Für den ersten Prototypen habe ich eine Grundplatte gezeichnet, welche von einem Mechaniker angefertigt wurde. Auf der Unterseite wurden die Motoren befestigt. Die Oberseite ist bestückt mit den Akkuhaltern und den Distanzbolzen, um weiter oben die Leiterplatte zu montieren.

Mechanische Zeichnung einfügen

## Regelungsalgorithmus

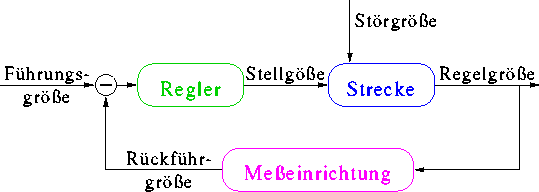
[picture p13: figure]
Bildergebnis für Regelung

Regelungstechnik ist ein grosser Teil des Projekts. Im Grundprinzip funktioniert jede Regelungsschaltung, ob digital oder analog, auf dem gleichem Grundprinzip. Die Differenz zwischen der Führungsgrösse, also dem gewollten Sollwert und der Rückführgrösse, also die gemessene tatsächliche Grösse, wird einem Regler übergeben. Dieser errechnet die Stellgrösse für den Aktor, welcher in die Regelstrecke eingreift. Ein Sensor misst die Regelstrecke aus. Über die Messeinrichtung wird die Rückführungsgrösse erzeugt und als Rückführgrösse Rückgekoppelt.

Abbildung 12: (Heuler, 2019)

Konkret auf den Balancer Robot angewendet lässt sich die Regelstrecke folgendermassen beschreiben: Abhängig von der errechneten Stellgrösse wird die Spannung über den Motoren reguliert. Durch äussere Störgrössen wie z.B. die Erdanziehungskraft kippt der Roboter in eine Richtung. Der Sensor detektiert die Veränderung des Winkels und somit die Abweichung vom Sollwert. Der Regler berechnet eine neue Stellgrösse um den falschen Winkel wieder zu korrigieren.

PID-Regler Prinzip

# Schluss

## Fazit

## Glossar

## Quellenverzeichnis

## Abbildungsverzeichnis

## Tabellenverzeichnis

# Dank

# Anhang

BMA-BalancerRobot.docx Seite 3 von 13

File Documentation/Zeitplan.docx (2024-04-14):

Start | Was | Dauer in h
09.09.2019 | Berchnen der Physikalischen Kräfte
15.09.2019 | Motoren, Sensoronen und Akkumulatoren bestellen
19.11.2019 | Dokumentation Haupteil fertig
22.11.2019 | Einleitung, Schlussteil, Reflexion fertig
26.11.2019 | Abgabe BMA | -

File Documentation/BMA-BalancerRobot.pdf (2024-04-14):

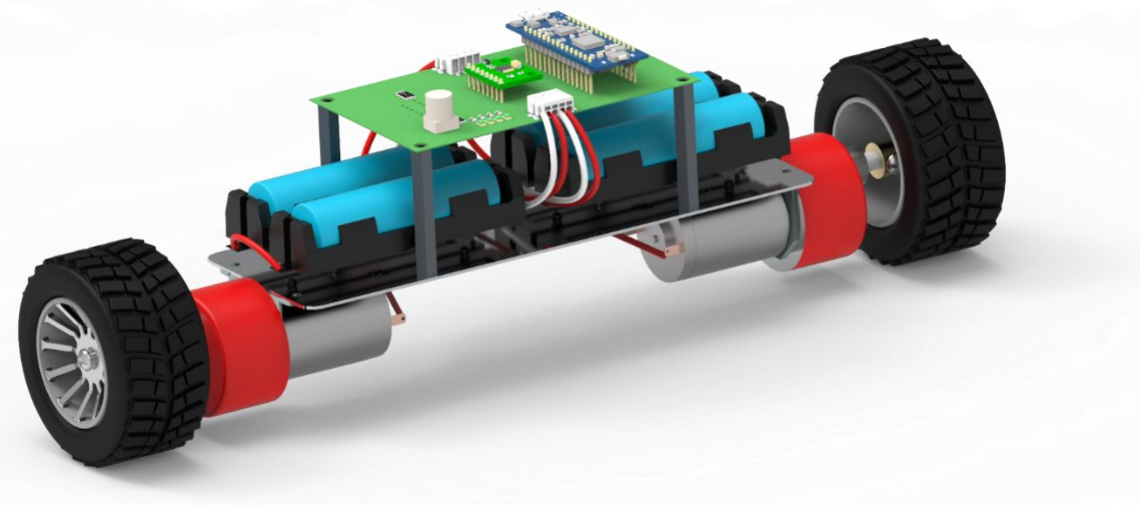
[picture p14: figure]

# BALANCER ROBOT

## Berufsmaturitätsarbeit

Lacher Markus, BEL16a

markuslacher@hotmail.ch

Berufsmaturitätsschule Zürich Technik, Architektur, Life Sciences

Betreuer: | H.P. Lutz
Abgabe: | 26.11.2019

Balancer Robot

M.Lacher | Seite 1 von 35

## Abstract

Im Projekt „Balancer Robot“ werden die physikalischen Effekte eines selbstbalancierenden Fahrzeugs analysiert. Ziel des Projekts ist die Entwicklung einen selbstbalancierenden Fahrzeugs.

Mithilfe von Testversuchen wird das Verhalten eines 3-Achsen Beschleunigungs- und Gyrosensors untersucht. Eine selbstentwickelte Elektronik steuert zwei DC-Bürstenmotoren an. Per Mikrocontroller wird der Sensor konfiguriert und ausgelesen. Nach der Verarbeitung der Daten werden die Motoren mithilfe eines Regelungsalgorithmus angesteuert mit dem Versuch, das Fahrzeug auszubalancieren.

Die Ergebnisse zeigen: Durch korrektes Verarbeiten der Sensorwerte lässt sich der Neigungswinkel des Fahrzeugs bestimmen. Durch eine PWM Ansteuerung können die Motoren reguliert werden. Doch erste Testversuche zeigen, dass für ein Ausbalancieren des Fahrzeugs nicht die Spannung über den Motoren, sondern die Stromaufnahme der Motoren reguliert werden sollte, da sich diese im Gegensatz zur Spannung proportional zum Drehmoment der Motoren verhält. Zudem wurde festgestellt, dass ein simpler PID-Regler als Regelungsalgorithmus nicht ausreicht, um das Fahrzeug auszubalancieren.

## Inhalt

## Einleitung

Fragestellung
Ist es möglich, mithilfe eines Beschleunigungs- und Gyrosensors und zwei DC-Motoren ein Fahrzeug auf 2 Rädern auszubalancieren? Welche physikalischen Kräfte wirken und wie funktioniert das Ausbalancieren?

In einem YouTube Video sah ich ein kleines selbstgebautes Fahrzeug, welches sich auf 2 Rädern ausbalanciert, indem es vorwärts und rückwärts fährt. Dieses Prinzip faszinierte mich so sehr, dass ich selber ein Fahrzeug bauen wollte, welches sich ausbalanciert.

Grosse Teile dieses Projekts befassen sich mit der Entwicklung einer Elektronik, welche die Sensorik und die Ansteuerung der Motoren zur Verfügung stellt, damit eine Regelungssoftware das Ausbalancieren des Fahrzeugs bewältigen kann. Es werden Überlegungen zur Physik angestellt, sowie Informationen über Regelungstechnik gesammelt, damit eine Elektronik entwickelt werden kann, die ein Ausbalancieren ermöglicht.

Projektphasen
Das Projekt lässt sich in folgende 4 Phasen unterteilen:
1) Berechnen, analysieren und verstehen der physikalischen Kräfte
Zu Beginn wurden physikalische Berechnungen durchgeführt, um die wirkenden Kräfte abzuschätzen.
2) Entwickeln der Elektronik und der Mechanik
Aufgrund der Überlegungen zur Physik wurden Motoren und Sensoren bestellt. Danach wurde ein erster Prototyp entwickelt.
3) Entwickeln der Embedded Software
Für den ersten Prototyp wurde Software entwickelt, welche die Hardware steuert. Dies beinhaltet das Konfigurieren und Auslesen des Sensors, das Ansteuern der Motoren, sowie das Überprüfen der Akku-Ladung. Zusätzlich wurde eine Software für den Computer entwickelt, dass die Messwerte des Sensors analysiert werden können.
4) Entwickeln eines Regelalgorithmus
Nachdem der erste Prototyp entwickelt wurde und die Software für das Steuern der Hardware programmiert und getestet wurde, konnten erste Balancier-Versuche mithilfe eines Regelungsalgorithmus durchgeführt werden. Ich informierte mich über PID-Regler und entwickelte einen ersten kleinen Regelungsalgorithmus. Leider mit begrenztem Erfolg, denn das Ausbalancieren funktionierte nur beschränkt.

Im Hauptteil werden diese 4 Phasen chronologisch abgearbeitet. Zuerst wird das grobe Konzept jeder Regelungselektronik sowie das physikalische Grundprinzip erläutert. Nachfolgend sind Information über die Sensorik und die Aktoren dokumentiert. Anschliessend ist die Entwicklung der Leiterplatte, der Mechanik und der Software beschrieben. Abschliessend sind erste Experimente eines Regelalgorithmus dokumentiert.

## Hauptteil

Konzept
Der Balancer Robot ist im Prinzip nichts anderes als eine Regelungselektronik. Über Sensorik wird eine physikalische Grösse gemessen und mithilfe der Regelung wird ein Aktor angesteuert, sodass sich ein gewollter Sollwert einstellt.

Das Fahrzeug misst mithilfe eines 3-Achsen Gyrosensors und eines 3-Achsen Beschleunigungssensors die Kräfte, die auf das Fahrzeug wirken. Die Messwerte werden von einem Mikrocontroller eingelesen und verarbeitet. Dieser versucht dann die Motoren so anzusteuern, dass das Fahrzeug nicht umfällt.

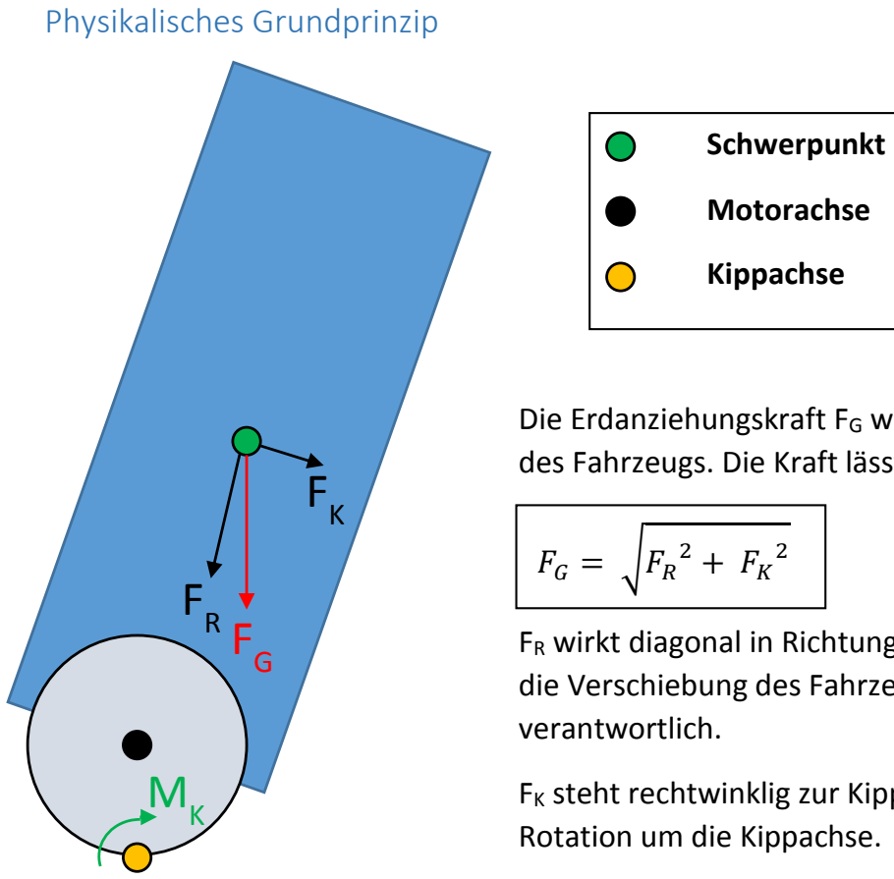
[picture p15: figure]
Physikalisches Grundprinzip; verantwortlich.; Rotation um die Kippachse.; Schwerpunkt; Motorachse; Kippachse

Die Erdanziehungskraft FG wirkt auf den Schwerpunkt des Fahrzeugs. Die Kraft lässt sich aufteilen in FR und FK.

FR wirkt diagonal in Richtung der Kippachse und ist für die Verschiebung des Fahrzeugs beim Umfallen

FK steht rechtwinklig zur Kippachse beschleunigt die

Diese Rotation resultiert in einem Drehmoment MK auf der Kippachse. Je schiefer das Fahrzeug steht, desto

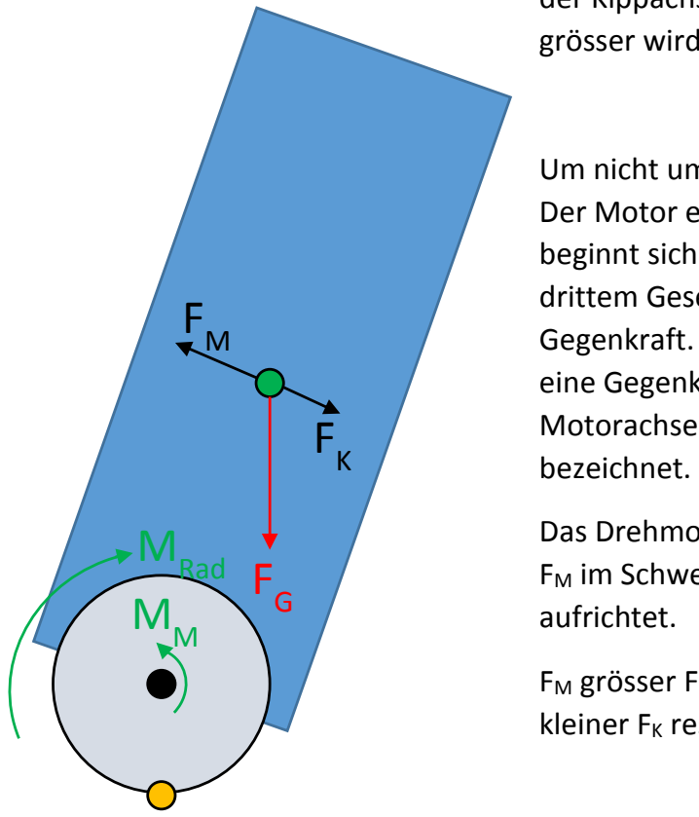
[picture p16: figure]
bezeichnet.; aufrichtet.; MRad

grösser wird FK und somit auch MK.

Um nicht umzufallen muss das Fahrzeug vorwärts fahren. Der Motor erzeugt das Drehmoment MRad, das Rad beginnt sich im Uhrzeigersinn zu drehen. Laut Newtons drittem Gesetz folgt auf eine Kraft immer eine Gegenkraft. Dies bedeutet, dass das Drehmoment MRad eine Gegenkraft, bzw. Gegendrehmoment auf die Motorachse ausübt. Diese Gegenkraft wird mit MM

Das Drehmoment MM der Motorachse erzeugt eine Kraft FM im Schwerpunkt, welche das Fahrzeug wieder

FM grösser FK resultiert im Aufrichten des Fahrzeugs, FM kleiner FK resultiert im Umfallen des Fahrzeugs.

Dividiert man das Drehmoment des Rades durch dessen Radius, erhält man die Kraft Fa, welche das Fahrzeug relativ zum Boden beschleunigt.

Die beschleunigende Kraft Fa ist wichtig, da die Reifen einen Reibungskoeffizienten besitzen. Die Gewichtskraft FG multipliziert mit dem Reibungskoeffizienten definiert die maximal mögliche Beschleunigungskraft Fa.

Der erste Prototyp wiegt 788g. Der Reibungskoeffizient des Reifen ist abhängig von der Oberfläche, auf der dieser rollt. Die Schätzung des Reibungskoeffizienten wurde für einen Holzboden als Unterlage getroffen, da der Prototyp hauptsächlich auf selbigem getestet wurde.

Schätzung Reifen auf Holzboden: µreifen (https://de.wikipedia.org/wiki/My) ≅ 0.75

Die Rechnung zeigt auf, dass ein Drehmoment von 0.203Nm pro Reifen nicht überschritten werden sollte, da dieser ansonsten die Haftung zum Boden verliert und durchdreht.

MM

MRad

F
a
r | Fa =

MRad
r

Fa ≤ FG ∗ µreifen (https://de.wikipedia.org/wiki/My)

Famax = 0.788kg ∗ 9.81

m
s

2

∗ 0.75 = 5.798N

MRadmax = 5.798N ∗ 35mm = 0.203Nm

Sensorik
Die rechts abgebildete Leiterplatte ist mit dem Sensor MPU-6050, einen sehr verbreiteten Gyro- und Beschleunigungssensor, bestückt. Dieser misst in allen 3-Achsen die Beschleunigung, sowie die Rotationsgeschwindigkeit. Über die digitale I2C Kommunikationsschnittstelle kann der Sensor konfiguriert und ausgelesen werden.

Rotation
Der Gyrosensor misst die Rotation um eine Achse in Grad/s.
Je nach Konfiguration kann der Sensor bis zu 1000°/s
messen. Befindet sich der Sensor in Ruhelage, ist die Rotation

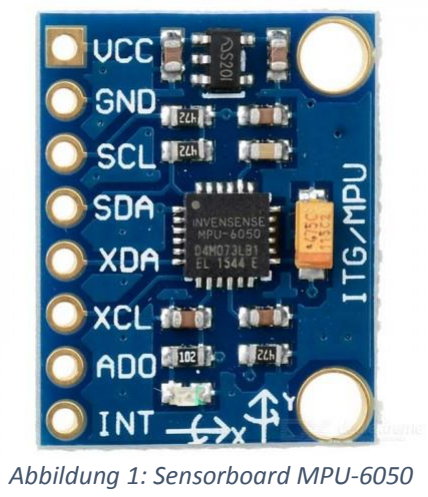
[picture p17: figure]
Abbildung 1: Sensorboard MPU-6050
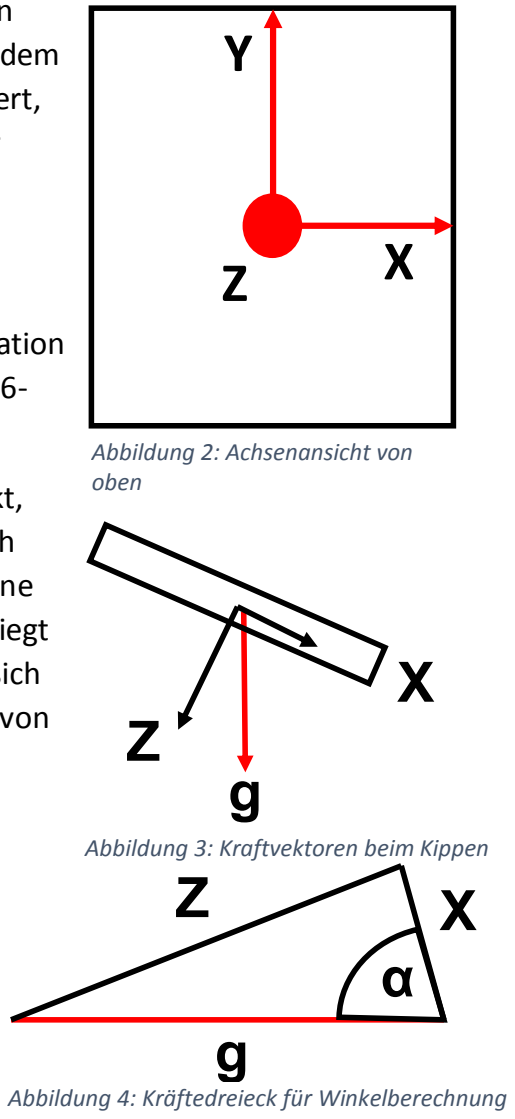
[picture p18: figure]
Abbildung 2: Achsenansicht von oben; Abbildung 3: Kraftvektoren beim Kippen Z

aller Achsen gleich 0. Man könnte den Winkel bestimmen, indem man die Rotationsgeschwindigkeit pro Zeiteinheit aufsummiert, jedoch driftet die Berechnung des Winkels ab, da Messfehler addiert werden und somit das Ergebnis mehr und mehr verfälscht wird.

Beschleunigung
Die Beschleunigung wird in m/s² gemessen. Je nach Konfiguration kann der Sensor bis zu +/- 16G messen, dass entspricht der 16-fachen Erdbeschleunigung also ca. 160m/s²

Liegt der Sensor still, ist die einzige Kraft, welche auf ihn wirkt, die Erdbeschleunigung. Würde der Sensor flach auf dem Tisch liegen wie in Abbildung 1, dann misst man auf der Z-Achse eine Beschleunigungskraft von 9.81m/s²
. Auf der X- und Y-Achse liegt keine Kraft an. Beginnt man nun den Sensor zu kippen, teilt sich die Kraft der Erdbeschleunigung auf die Achsen auf. Mithilfe von Vektorgeometrie lässt sich dann der Winkel bestimmen.

Um den Roboter auszubalancieren versucht die Regelung den Winkel Alpha immer bei 90° zu halten.

Konfiguration
Der Sensor wird so konfiguriert, dass er mit einer Frequenz von 100Hz die Messwerte der 6-Achsen aufzeichnet. Sobald diese bereit zum Auslesen sind, wird dies über den Pin INT (Interrupt) signalisiert. Die Messwerte werden dann sofort vom Mikrocontroller ausgelesen und verarbeitet.

Abbildung 4: Kräftedreieck für Winkelberechnung

∝ = arctan (

Z
X

)

Datenverarbeitung
Der Sensor besitzt einen internen DMP. Richtig konfiguriert filtert dieser die Messdaten mit einem Tiefpassfilter, damit Störungen bereits intern im Sensor herausgefiltert werden können.

Auch per Software werden die Daten nochmals optimiert. Das Daten Verarbeiter Modul der Software glättet die Messwerte mithilfe eines gleitenden Mittelwerts.

Durch das Tiefpassfilter und den gleitenden Mittelwert werden Störungen, Messfehler und Rauschen des Sensor minimiert.

Einziger Nachteil: Durch das Verarbeiten der Daten wird die Zeitverzögerung der tatsächlichen Messung bis zu deren Verarbeitung durch Regler grösser. Dies kann das Verhalten des Reglers negativ beinflussen.

Abbildung 5:Blockschema MPU-6050 (InvenSense, 2019)

Abbildung 6: Gleitender Mittelwert (Wikipedia, 2019)

Sensor Auswertung
Um den Sensor zu testen wurde eine erste Testsoftware für den Mikrocontroller geschrieben, welche die gemessen Werte über die UART-Schnittstelle des Mikrocontrollerboards an einen angeschlossenen PC sendet. Zusätzlich wurde eine Python Software entwickelt, welche die gesendeten Daten verarbeitet und diese in eine Excel Tabelle schreibt. Dadurch konnte das Verhalten des Sensors analysiert werden.

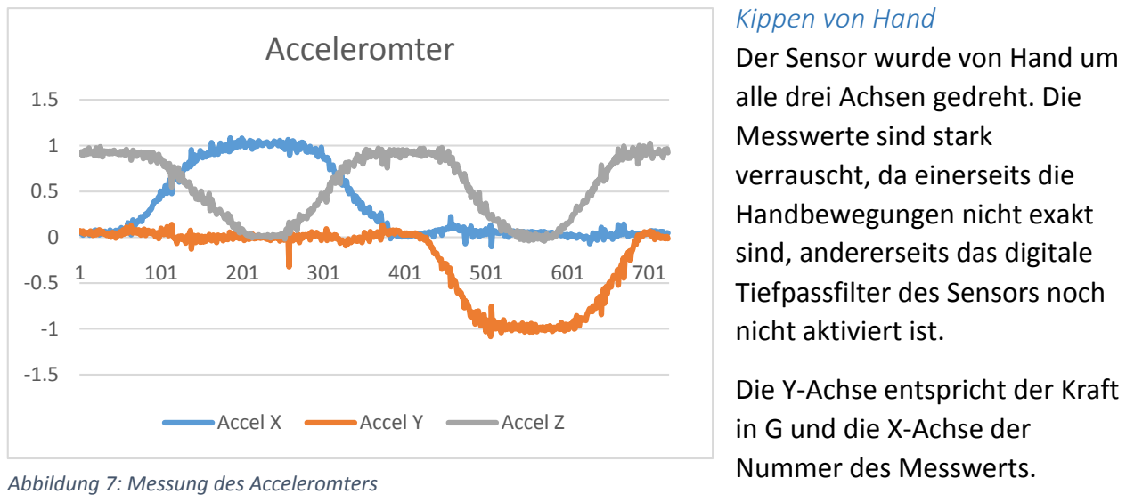
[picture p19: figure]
Kippen von Hand Der Sensor wurde von Hand um alle drei Achsen gedreht. Die Messwerte sind stark verrauscht, da einerseits die Handbewegungen nicht exakt sind, andererseits das digitale Tiefpassfilter des Sensors noch nicht aktiviert ist.; Die Y-Achse entspricht der Kraft in G und die X-Achse der Nummer des Messwerts.; Acceleromter; Accel X; Accel Y; Accel Z; Abbildung 7: Messung des Acceleromters
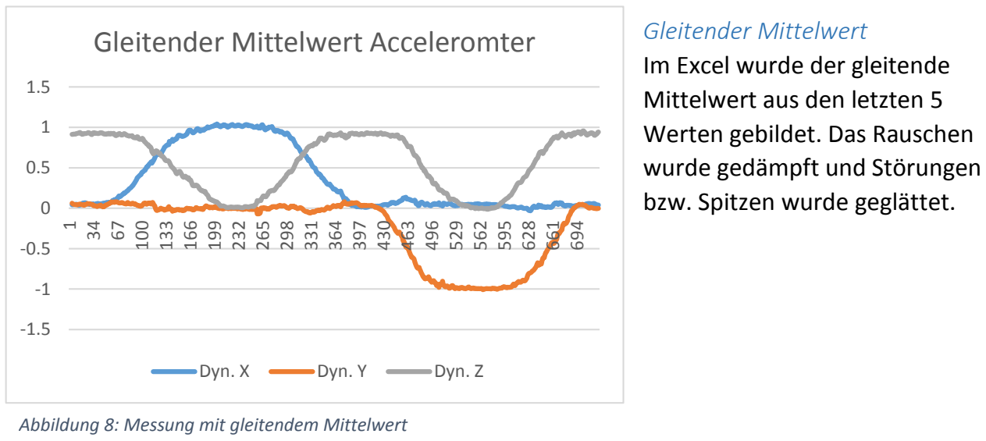
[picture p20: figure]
Gleitender Mittelwert Im Excel wurde der gleitende Mittelwert aus den letzten 5 Werten gebildet. Das Rauschen wurde gedämpft und Störungen bzw. Spitzen wurde geglättet.; Gleitender Mittelwert Acceleromter; Dyn. X; Dyn. Y; Dyn. Z

Abbildung 8: Messung mit gleitendem Mittelwert

Um zu prüfen ob der Sensor den Anforderungen entspricht und auch um ein Verständnis für das Verhalten des Sensors zu entwickeln wurden zwei weitere Tests durchgeführt.

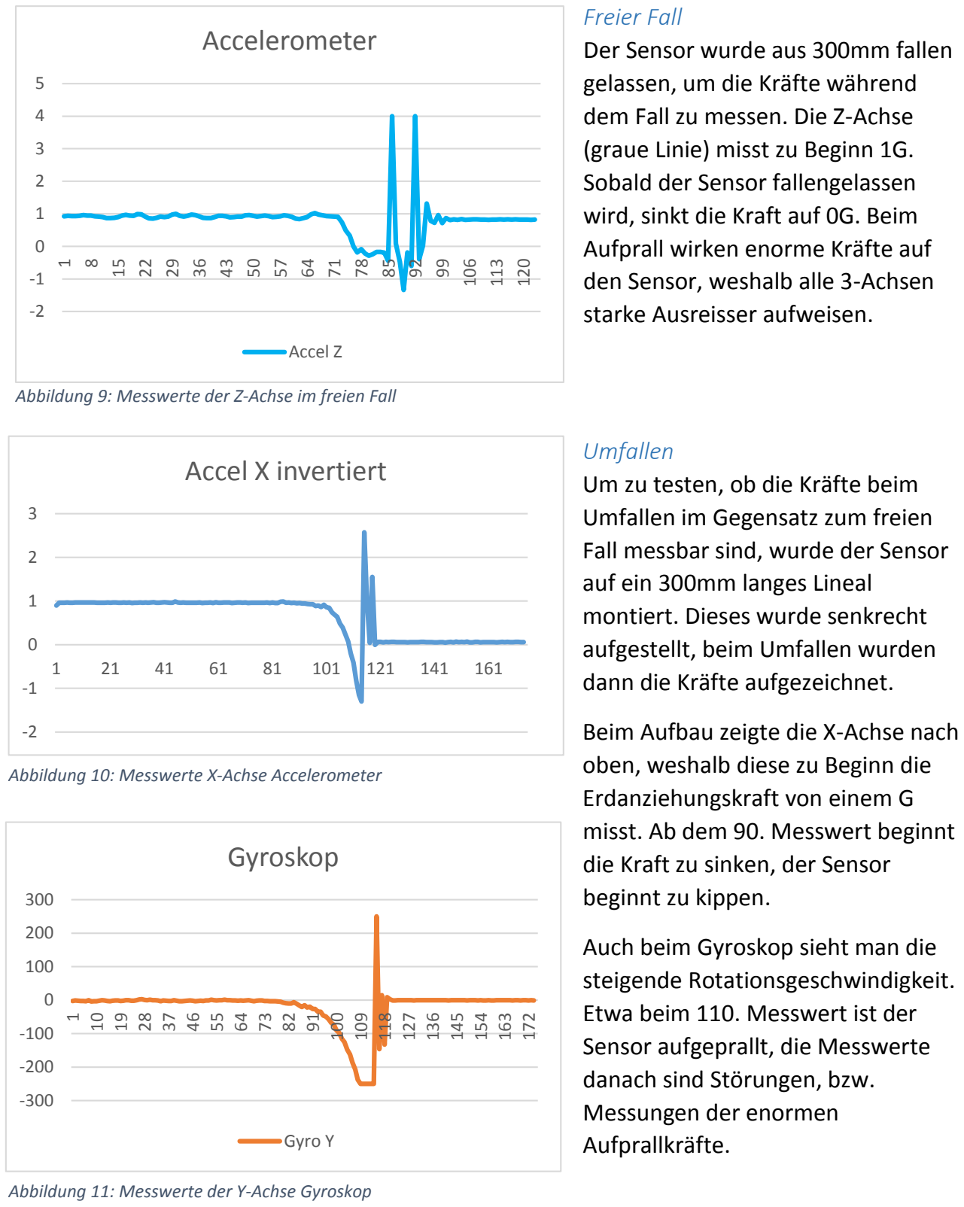
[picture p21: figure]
Freier Fall Der Sensor wurde aus 300mm fallen gelassen, um die Kräfte während dem Fall zu messen. Die Z-Achse (graue Linie) misst zu Beginn 1G. Sobald der Sensor fallengelassen wird, sinkt die Kraft auf 0G. Beim Aufprall wirken enorme Kräfte auf den Sensor, weshalb alle 3-Achsen starke Ausreisser aufweisen.; Umfallen Um zu testen, ob die Kräfte beim Umfallen im Gegensatz zum freien Fall messbar sind, wurde der Sensor auf ein 300mm langes Lineal montiert. Dieses wurde senkrecht aufgestellt, beim Umfallen wurden dann die Kräfte aufgezeichnet.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

Interessant zu beobachten ist, dass die Kurve beim Beschleunigungssensor nicht bei 0G stoppt, da dies ja einem Winkel α von 0° entsprechen würde. Dies ist auch auf die Kräfte beim Aufprall zurückzuführen. Nachdem der Sensor ruhig auf dem Boden liegt, sieht man auch die erwartete Kraft von 0G.

Abbildung 10: Messwerte X-Achse Accelerometer

Abbildung 9: Messwerte der Z-Achse im freien Fall

Abbildung 11: Messwerte der Y-Achse Gyroskop

Aktoren
Ansteuerung Motor
Ein DC-Motor besitzt zwei Anschlüsse. Ändert die Richtung des Stromes, wechselt auch die Drehrichtung des Motors. Um dieses Wechseln des Stromes elektronisch umzusetzen wurde eine H-Brücke, auch Vierquadrantensteller genannt, verwendet.

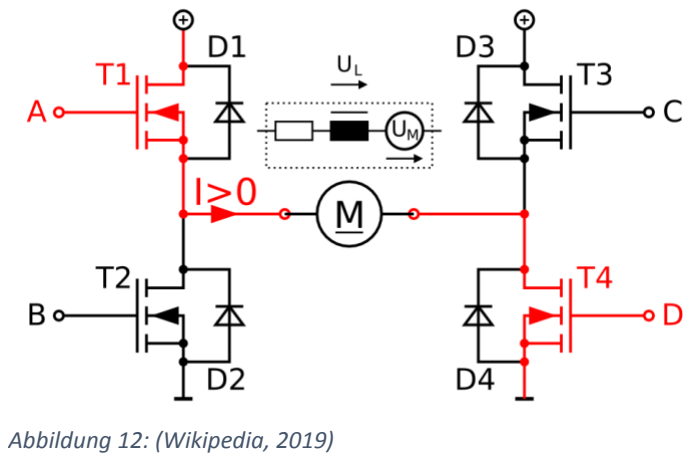
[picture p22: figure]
Abbildung 12: (Wikipedia, 2019)

Prinzip: Die Schaltung besitzt eine Motorspannung U+ und einen GND. Schaltet der Transistor T1 und T4 während T2 und T3 sperren, dann liegt vom linken zum rechten Anschluss des Motors gesehen eine positive Spannung an.

Sperrt T1 und T4 und leiten dafür T2 und T3, dann liegt eine negative Spannung vom linken zum rechten Anschluss an. Die Drehrichtung ändert.

Da ich die Anschlüsse A-D der H-Brücke mit CMOS-Logik (0 – 3.3V, gegeben durch Mikrocontroller) ansteuern möchte, die Motorspannung U+ jedoch bis zu 16V beträgt, müssten für den Anschluss A und C noch zusätzliche Komponenten für die Spannungstransformation verwendet werden. Ausserdem bräuchten die Bauteile einzeln verbaut mehr Platz. Deswegen wird der IC L293D verwendet.

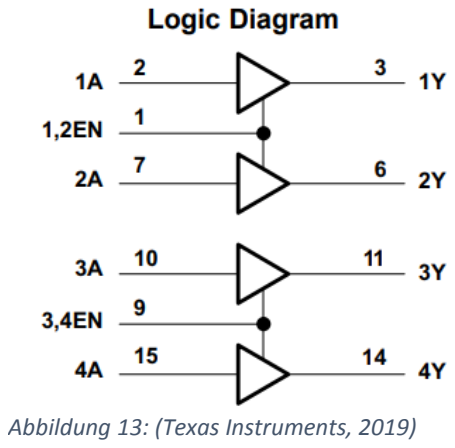
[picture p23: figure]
Abbildung 13: (Texas Instruments, 2019)

Der Baustein besitzt 4 High-Voltage Treiber. Über den Eingang A kann mit 0V oder 3.3V der Ausgang Y auf 0V oder auf den Level der Speisespannung geschaltet werden. Die Speisespannung kann bis zu 36V betragen. So kann an 1Y und 2Y der erste Motor und über 3Y und 4Y der zweite Motor angeschlossen werden.

Die Ausgänge können bis zu 1.2A liefern und auch „schlucken“. Mit den beiden Signalen 1,2EN und 3,4EN können die Treiber aktiviert werden.

PWM
Die Software soll die Leistungsabgabe des Motors steuern können, ansonsten ist eine Regelung nicht möglich. Um diese Steuerung zu erreichen wird die H-Brücke mit einem PWM Signal angesteuert. PWM steht für Pulse Wide Modulation.

Die Spannung über dem Motor soll reguliert werden. Da die Hardware jedoch nur zwei Zustände einstellen kann, (siehe H-Brücke) wird mit ständigem Ein- und Ausschalten die Spannung über dem Motor reguliert.

Abbildung 14: (Mikrocontroller.net, 2019)

T = tein + taus

f =

1
T

Tastgrad =

tein
T

Motor Stromaufnahme
Problem
Die ersten Tests mit dem L293D mit PWM Ansteuerung verliefen gut. Die Motoren liessen sich in beide Richtungen drehen. Der L293D wurde aber relativ heiss. Doch als ich den Roboter das erste Mal zusammengebaut hatte und diverse Probleme nach einer zeitintensiven Fehlersuche endlich beheben konnte, wollte ich die komplette Software mit einem einfachen Regelungsalgorithmus testen.

Der L293D Baustein wurde noch heisser als sonst und ein Motor arbeitete nicht richtig. Ich vermutete der Baustein sei beschädigt, da ich ihn anfangs falsch angeschlossen hatte. Als ich den Baustein austauschte in der Hoffnung, die Ansteuerung der Motoren würde funktionieren, ging dieser direkt bei Einschalten der Motoren kaputt, der Mikrocontroller funktionierte auch nicht mehr.

Theorie
Im Projekt werden Gleichstrom- Bürstenmotoren eingesetzt. Diese erzeugen durch die Rotation der Achse eine Gegeninduktion in der Spule, welche den Strom ausbremst. Je höher die Drehzahl des Motors, desto grösser ist die Gegenspannung und dementsprechend wird der Strom umso kleiner. Dies ist auch der Grund für die Tatsache, dass das Drehmoment bei Elektromotoren bei steigenden Drehzahlen abnimmt.

Analyse

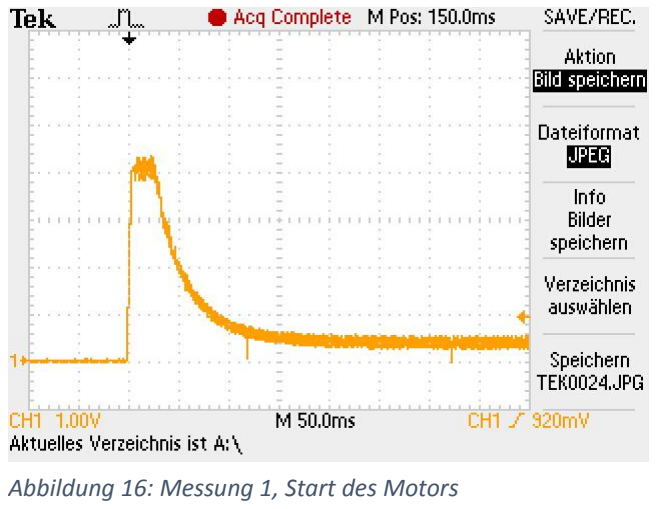
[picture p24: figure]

Um das Problem zu analysieren wurde ein Messversuch durchgeführt. Über einen 2 Ohm Messwiderstand wurde mithilfe eines Oszilloskops die Stromaufnahme des Motors aufgezeichnet. Dieser ist nicht ideal, da der Ohm’sche Widerstand der Motorspule 3Ohm beträgt. Dies führt bei grossen Strömen zur Verminderung der Spulenspannung über dem Motor, da über dem Messwiderstand eine zu grosse Spannung abfällt.

Trotzdem war der Fehler bereits nach der ersten Messung offensichtlich. Im Stillstand induziert die Motorwelle in der Spule noch keine Gegenspannung. Beim Einschalten wirkt somit ganz kurz die Impedanz der Spule, danach nur noch der Ohm’sche Widerstand von 3Ω. Bei 15V entsteht dann über einen Zeitbereich von 40ms ein Strom von über 4 Ampère. Danach sinkt der Strom innerhalb von 60ms auf 200mA. Dies entspricht ziemlich genau den Angaben des Datenblatts, welches bei keiner mechanischen Belastung einen Strom von 180mA angibt.

+ UMotor 15

L

R

RMess 2

V +

Oszilloskop

Abbildung 15: Messaufbau | Abbildung 16: Messung 1, Start des Motors

Parameter:

U0: | 15V
RMess | 2Ω
RMotor | 3Ω

Der Motortreiber L293D kann pro Ausgang einen konstanten Strom von 1.2A Ampère liefern, was für den Normalbetrieb des Motors ausreichen würde. Doch der kurzzeitige Stromspitz beim Anfahren genügt, um den Motortreiber zu zerstören.

Um der hohen Stromanforderung gerecht zu werden, wurde ein neues IC getestet. Der L298 ist ähnlich aufgebaut wie der alte Treiber L293D, jedoch kann dieser einen Strom von 2A liefern und kurzzeitige Spitzen bis zu 3A Ampère. Dieser wird im Betrieb auch sehr warm, funktioniert jedoch.

Strommessung bei Anfahren mithilfe von PWM. Man sieht die PWM Frequenz von 1kHz sowie das Stromverhalten eines LC Gliedes, da die Kurve einer e-Funktion ähnelt. Da die Spannung nur kurzeitig eingeschaltet ist, steigt der Strom nicht über 1.5A, weshalb der L293D intakt bleibt.

Gefährlich wird es, wenn der Motor mit einem hohen PWM Wert anfährt.

Messung des Stroms bei laufendem Motor mit einem PWM von 60%. Man sieht gut, dass der Motor im Betrieb weniger Leistung benötigt als beim Anfahren. In der Messung sieht man auch gut, wie der PWM arbeitet. Die negativen Stromspitzen werden beim Abschalten der Spule durch deren Selbstinduktion erzeugt.

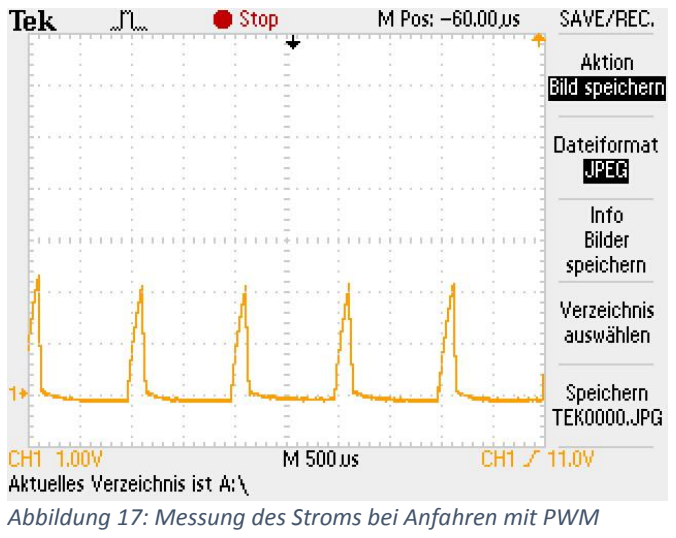
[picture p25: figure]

Abbildung 17: Messung des Stroms bei Anfahren mit PWM

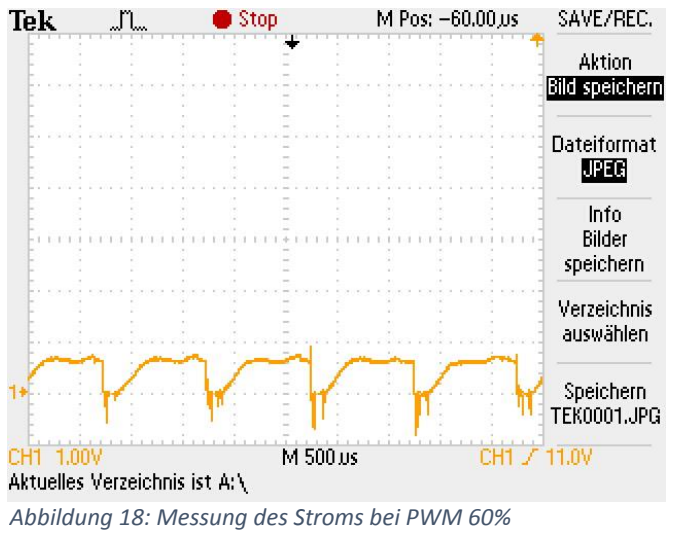
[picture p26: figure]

Abbildung 18: Messung des Stroms bei PWM 60%

L298 als neuer Motortreiber
Die Messungen zeigten, dass sich der L298 aufgrund der grösseren Ausgangsleistung besser für die Ansteuerung der Motoren eignet. Dieser IC hat ein grösseres Gehäuse mit besserer Kühlfläche und 2 zusätzliche Anschlüsse. Im Gegensatz zum L293D sind die Emitteranschlüsse der beiden H-Brücken nicht direkt mit GND verbunden, sondern über zwei Pins hinausgeführt. Dies ermöglicht das Einsetzen zweier Shunt Widerstände um die Stromaufnahme der beiden Motoren zu messen.


Abbildung 19: Block Diagramm aus L298 Datenblatt (ST Microelectronics, 2019). Die roten Kreise markieren die beiden

Layout
Von Beginn an war klar, dass eine Leiterplatte entwickelt werden muss, damit die vielen Verbindungen nicht mit Kabel umgesetzt werden müssen. Die erste Idee war das Entwickeln zweier Leiterplatten. Eine Leiterplatte ist mit dem Motortreiber bestückt und wird vom Akku gespiesen. Auf der zweiten Leiterplatte befinden sich die Sensorik, der Mikrocontroller sowie der Taster für den Benutzer. Die beiden Leiterplatten sollten übereinander verbaut werden, der Motor Driver zwischen den Akkus und das Controller Board oberhalb davon.

Abmessung: 50x50mm

Da die Akkuhalter sehr lang sind würde das Fahrzeug viel zu breit werden. Deshalb wurde eine zweite Variante entwickelt, in der alle Komponenten auf einer Leiterplatte bestückt sind. Dies vereinfacht einerseits die Verdrahtung der einzelnen Fahrzeugkomponenten, andererseits konnte die Breite des Fahrzeugs um 50mm verringert werden.

Abmessung: 100x60mm

Abbildung 22: Leiterplatte "Balancer Robot V1.00"

Abbildung 21: Leiterplatte „Controller Board V1.00“

Abbildung 20: Leiterplatte „Motor Driver V1.00“


Nachdem dem die Probleme mit dem Motortreiber L293D auftraten und ein neuer Treiber evaluiert wurde, musste eine neue Leiterplatte entwickelt werden. Rot eingekreist sieht man den neuen Motortreiber sowie die beiden Shunt-Widerstände für die Strommessung.

Die Bohrungen haben einen Durchmesser von 4.3mm und sind somit für M4 Schrauben ausgelegt. Das Zentrum der Bohrungen ist 4mm vom Rand entfernt.

Abbildung 24: Leiterplatte "Balancer Robot V1.01"

Abbildung 23: Mode-Taster

Ganz rechts auf dem Layout befindet sich ein Taster. Mithilfe dieses Tasters kann der Benutzer die Software steuern. Im fertigen Produkt wird dann der Mode des Balancer Robots geändert.

Die 4 LED signalisieren dem Benutzer folgende Informationen:

Batt: Batteriespeisung vorhanden VCC: 3.3V Speisung vorhanden
Mode: Signalisiert den aktuellen Modus mithilfe eines Blink-Codes
Error: Signalisiert verschiedene Fehler mithilfe eines Blink-Codes

Abbildung 25: LED-Anzeige


Über den Akku-Stecker wird die Schaltung eingespeist. Jeweils zwei Anschlüsse für das positive Spannungspotential und zwei Anschlüsse für das negative Spannungspotential sind miteinander verbunden. Dies ermöglicht einerseits das Weiterführen der Akkuspannung, andererseits können bei grosser elektrischer Belastung zwei Drähte parallel zur Einspeisung verwendet werden.

Abbildung 26: Akku-Stecker

An den 4 Anschlüssen des Motor-Steckers werden die beiden Motoren angeschlossen. Pro Motor ist ein Anschluss mit Plus und ein Anschluss mit Minus gekennzeichnet. Auf der mechanischen Grundplatte sind diese Bezeichnungen wiederzufinden.

Es ist wichtig, dass die Motoren korrekt angeschlossen werden, ansonsten funktioniert das Ausbalancieren nicht.

Abbildung 27: Motor-Stecker

Abbildung 28: L298 Motor
Treiber

Der neue Motortreiber L298 ist senkrecht aufgerichtet, damit auf der Rückseite ein Kühlkörper montiert werden kann.

Die beiden Shunt-Widerstände sind so nahe wie möglich am dazugehörigen Pin und danach direkt auf GND angeschlossen, damit der Widerstand der Leiterbahnen möglichst gering bleibt.

Ein SMD-Elektrolytkondensator stützt die Akkuspannung, direkt beim Motor Treiber, damit diese bei schnell ändernder Belastung nicht zusammenbricht.

Abbildung 29: Seitenansicht, Rückseite des L298

Das Sensorboard kann in dieser Ausführung online bestellt werden. Es ist bestückt mit dem Beschleunigungs- und Gyrosensor MPU6050 sowie einem Längsregler für die Spannungsversorgung plus diverser zusätzlicher Hardware.

Dieses Board kann so direkt auf den Print gesteckt werden. Dies erleichtert ein allfälliges Ersetzen des Sensors bei einem Defekt. Zusätzlich könnte später ein eigenes Sensorboard entwickelt werden mit zusätzlichen Features, welches dann das aktuelle ersetzt.

Abbildung 30: Sensorboard MPU-6050
Abbildung 31: Mikrocontrollerboard STM32F303K8

Das Mikrocontrollerboard Nucleo STM32F303K8 ist ein Entwicklungsboard von STMicroelectronics. Es stellt alle nötigen Peripheriebauteile für das Verwenden eines Mikrocontrollers zur Verfügung.

Das Mikrocontrollerboard kann direkt auf den Print gesteckt werden. Dies erleichtert ein allfälliges Ersetzen des Mikrocontrollers bei einem Defekt.

Akkumulatoren
Für die Energieversorgung der Elektronik werden handelsübliche Lithium-Ionen Akkuzellen verwendet.

Lithium-Ionen Akkuzellen, auch Li-Ion Akkus genannt, zeichnen sich durch eine sehr hohe spezifische Energiedichte aus, etwa 150 Wh/kg. Auch die Energiedichte von 400 Wh/l macht die Li-Ion Akkus interessant für mobile Anwendungsbereiche. (Wikipedia, 2019)

Nachteil: Die Akkuzellen sind anfällig auf Tiefenentladung sowie Überladung. Es ist also Elektronik notwendig sowohl für das Laden der Akkus, als auch für die Überwachung während des Betriebs.

Die Li-Ion Akkus werden von der Firma NKON aus den Niederlanden geliefert. Der Hersteller garantiert einen maximalen konstanten Strom von 10A, was für die Anwendung völlig ausreichend ist. Obwohl LI-Ion Akkus theoretisch von 4.3V bis runter zu 2.5V schädigungsfrei betrieben werden könnten, empfiehlt der Hersteller eine Spannung von 3V nicht zu unterschreiten.

Ein Spannungsteiler auf der Leiterplatte teilt die Akkuspannung mit dem Verhältnis 1:4.3, sodass der Mikrocontroller per AD-Wandler die Spannung
überwachen kann. Sollte die Spannung unter 3.2V
pro Zelle sinken, deaktiviert die Software die

Motoren, um den Energieverbrauch drastisch zu senken. Eine niedrige Akkuspannung wird mit einem 1Hz Blinken der Error LED signalisiert.

Abbildung 34: Spannungsteiler auf der Leiterplatte

Ingesamt werden 4 Akkuzellen in Serie geschaltet,
das ergibt eine Versorgungsspannung zwischen
12V – 16.8V. Mit einer Mindestkapazität von 2600mAh ergibt folgende ungefähre Energie:

Bei einem geschätzten durchschnittlichen Verbrauch von 0.8A ergibt das eine Betriebsdauer von über 3h.

Abbildung 32: Li-Ion Akkuzelle Typ 18650

Abbildung 33: Angaben der bestellten Akkuzellen (NKON,

W = U ∗ Q = 14.4V ∗ 2.6Aℎ = 37.44Wℎ

t =

W
P

=

37.44Wℎ
14.4V ∗ 0.8A

= 3.25ℎ

Mechanik
Die Mechanik spielt eine entscheidende Rolle im Projekt. Der Roboter sollte möglichst leicht sein, damit das benötigte Drehmoment, um den Roboter wieder aufzurichten, möglichst klein bleibt. Ausserdem muss auf die Gewichtsverteilung geachtet werden, um den Schwerpunkt tief zu halten.

Für den ersten Prototyp habe ich eine Grundplatte gezeichnet, welche von einem Mechaniker angefertigt wurde. Auf der Unterseite wurden die Motoren befestigt. Die Oberseite ist bestückt mit den Akkuhaltern und den Distanzbolzen, um weiter oben die Leiterplatte zu montieren.

Motor
MFA 950D501
Lieferant | Conrad.ch
Preis | 25.95 CHF
Betriebsspannung | 9-15V
Gewicht | 156g
Wellen-Länge | 15mm
Wellen-Durchmesser | 6mm
Untersetzung | 50:1
Maximale Effizienz | 61.85%
Leistungsabgabe maximale Effizienz (12V) | 6.21W
Stromaufnahme maximale Effizienz (12V) | 0.837A
Anfahrdrehmoment (12V) | 2.025Nm
Drehmoment bei maximaler Effizienz (12V) | 0.346Nm
Maximale Drehzahl (12V) | 252U/min
Drehzal bei maximaler Effizienz (12V) | 185.6U/min

Zu Beginn des Projekts wurden zwei verschiedene Motoren ohne Übersetzung auf Conrad.ch bestellt. Doch nach weiteren mechanischen Berechnungen wurde klar, dass das
Drehmoment der bestellten Motoren viel klein ist (ca. 0.1Nm). Deswegen wurde ein Motor mit mechanischer Übersetzung bestellt. Dieser besitzt ein Getriebe mit einer Untersetzung von 50:1. Dadurch wird das Drehmoment des Elektromotors mit dem Faktor 50 erhöht, respektive die Drehzahl um den Faktor 50 reduziert. Die mechanischen Verluste des Getriebes sind dabei vernachlässigbar. Der Motor arbeitet linear von 6V bis 15V. Das heisst bei 15V Spannung beträgt das Anfahrdrehmoment sogar 2.531Nm.

Abbildung 35: MFA 950D501 (Conrad, 2019)


Prototyp
Nachdem die Motoren bestellt waren, wurde zeitgleich zur Leiterplatte die Grundplatte aus Aluminium gezeichnet. Diese wurde dann von einem Mechaniker hergestellt. Nachdem die Leiterplatte bestückt wurde, konnte ein erster Prototyp zusammengebaut werden.

Abbildung 37: Erster Prototyp, Seitenansicht

Abbildung 36: Erster Prototyp, Vogelperspektive

3D-Modell
Der Prototyp besteht aus folgenden Komponenten:
1) Leiterplatte (aktuelle Version 1.01)
2) Distanzbolzen, Kunststoff M4 (aktuelle Länge 8mm)
3) 2x Akkuhalter für 4 Akkuzellen Typ 18650
4) Grundplatte, Aluminium
5) 2x Reifen, Durchmesser 70mm + Adapter für die Motorachse
6) 2x Bürstenmotor MFA 950D501


Abbildung 38: 3D-Modell Explosionszeichnung

Software; MPU6050 Treiber; Daten Verarbeiter; Regler; Motor Treiber; MPU6050; Interrupt; Kommunikation; Sensordaten; Aufbereitete Daten; Stellgrösse; PWM

Architektur
Blau: | Sensoren
Grün: | Mikrocontroller (Software)
Rot: | Aktoren

Der MPU6050-Treiber konfiguriert den Sensor, sodass dieser mit einer Frequenz von 100Hz die 3-Achsen des Gyrosensores, sowie die 3-Achsen des Accelerometers misst. Über einen Interrupt Pin wird dem Mikrocontroller signalisiert, dass die Daten bereitstehen. Der Mikrocontroller liest dann sofort die Daten aus.

Die Sensordaten werden dem Datenverarbeiter übergeben. Dieser berechnet den dynamischen Mittelwert der Daten, um diese zu Glätten und Störungen herauszufiltern.

Die aufbereiteten Daten werden dem Regler übergeben. Dieser errechnet mithilfe des Regelalgorithmus die Stellgrösse für die Motoren.

Die Stellgrösse wird dem Motortreiber übergeben. Aufgrund der Stellgrösse steuert der Motor Treiber die Motoren per PWM Signal an.

Regelungsalgorithmus
Allgemein
Die Regelungstechnik bildet einen grossen Teil des Projekts. Im Grundprinzip funktioniert jede Regelungsschaltung, ob digital oder analog, auf dem gleichem Grundprinzip. Die Differenz Xd zwischen der Führungsgrösse, also dem gewollten Sollwert und der Rückführgrösse, also die gemessene tatsächliche Grösse, wird einem Regler übergeben. Dieser errechnet die Stellgrösse für den Aktor, welcher in die Regelstrecke eingreift. Ein Sensor misst die Regelstrecke aus. Über die Messeinrichtung wird die Rückführungsgrösse erzeugt und rückgekoppelt.

Konkret auf den Balancer Robot angewendet lässt sich die Regelstrecke folgendermassen beschreiben: Abhängig von der errechneten Stellgrösse wird die Spannung über den Motoren reguliert. Durch äussere Störgrössen, wie z.B. die Erdanziehungskraft, kippt der Roboter in eine Richtung. Der Sensor detektiert die Veränderung des Winkels und somit die Abweichung vom Sollwert. Der Regler berechnet eine neue Stellgrösse um den falschen Winkel wieder zu korrigieren.

Abbildung 39: (Heuler, 2019)

PID-Regler
PID-Regler sind weit verbreitet in der Regelungstechnik. Sie lassen sich in folgende drei Grundanteile einteilen:

Proportional-Anteil
Der P-Anteil gibt proportional zur Regeldifferenz Xd eine Ausgangswert Y aus. P-Regler reagieren sofort auf Änderungen, können dafür die Regeldifferenz xd nicht vollständig ausregeln. KP definiert den P-Anteil der gesamten Regelung.

Integral-Anteil
Der I-Anteil integriert die Regeldifferenzen auf. Dadurch steigt bei einer konstanten Abweichung zwischen xd und dem Sollwert der Ausgang so lange an, bis die Differenz ausgeregelt wurde. KI definiert den I-Anteil der gesamten Regelung.

Differenzial-Anteil
Der D-Anteil differenziert die Regeldifferenzen. Dadurch reagiert der D-Anteil auf schnelle Änderungen der Regeldifferenz xd. Der D-Anteil alleine kann eine Regeldifferenz nicht ausregeln, wird jedoch verwendet, wenn schnelle Reaktionen auf Störsignale und Regeldifferenzabweichungen nötig sind. KD definiert den D-Anteil der gesamten Regelung.

Kombiniert sieht die Formel für den PID-Regler folgendermassen aus:

Die drei Regelanteile KP, KI und KD müssen abhängig der Anforderungen evaluiert werden. Eine grundsätzliche Faustregel besagt, dass der P-Anteil etwa 90% der Regelung übernimmt, der I-Anteil die bleibende Regeldifferenz sowie konstante Abweichungen mit der Zeit korrigiert werden. Der D-Anteil sollte so ausgelegt werden, dass Störungen und schnelle Abweichungen vom Sollwert abgefangen werden.

y = KP ∗ xd

y = KI ∗ ∫ xd∆t

t

0

y = KD ∗

∆xd
∆t

y = KP ∗ xd + KI ∗ ∫ xd∆t

t

0

+ KD ∗

∆xd
∆t

Umsetzung
In den ersten Versuchen wurde ein simpler P-Regler implementiert. Es wurde nicht ein tatsächlicher Winkel verwendet, sondern direkt die beschleunigende Kraft auf der Y-Achse. Denn die Kraft auf der Y-Achse ist direkt proportional zum nötigen Drehmoment für das Aufrichten.

Erster Versuch
Der Balancer Robot zitterte unaufhörlich und konnte sich selber nicht stabilisieren. Nach diversen Spielereien und Tests an den Regelparametern und der Sensordatenverarbeitung wurde dann folgender Denkfehler klar: Die Regelung der Motoren funktionierte gut, wenn dieser von Hand gekippt wird, doch wenn das Fahrzeug sich selbst aufrichtet, entstehen beschleunigende Kräfte, die jener der Y-Achse gegengerichtet sind. Der Balancer Robot möchte also ständig den Winkel korrigieren, beeinflusst aber direkt den Messwert durch die Korrektur, was eine Richtungsänderung zur Folge hat.

Korrektur der Beschleunigungskräfte
Da kommt der Gyrosensor ins Spiel. Die Messwerte des Beschleunigungssensors müssen korrigiert werden, damit der Winkel trotz der wirkenden Kräfte beim Aufrichten korrigiert werden kann.

Durch die Rotationsgeschwindigkeit, gegeben durch den Gyrosensor, und dem Radius zur Motorachse kann die Bahngeschwindigkeit des Sensors bestimmt werden.

Aus der Geschwindigkeitsänderung pro Zeit kann dann die verursachte Beschleunigung errechnet werden.

Subtrahiert man die durch die Aufrichtung entstehende Beschleunigung der Y-Achse, dann bleibt nur noch die Kraft der Erdbeschleunigung übrig.

Zweiter Versuch mit korrigiertem Messwert
Nachdem die Korrektur der Messwerte vorgenommen wurde, war eine klare Verbesserung zu sehen. Der Balancer Robot zitterte nicht mehr wie wild umher, sondern versuchte sich tatsächlich entgegen der Kipprichtung aufzurichten. Jedoch klappte das Ausbalancieren noch nicht, da der Roboter nach kurzer Zeit entweder durch ständiges Hin- und Herschwingen umfiel, oder aber bei Anpassungen des Proportionalfaktors zu schwach oder zu spät eingriff.

PID-Regler
Etwas Zeit war noch übrig, sodass noch ein PID-Regler programmiert werden konnte. Es wurden mehrere Versuche mit verschiedenen Werten der P-, I- und D-Anteile getestet. Doch das Ausbalancieren funktionierte auch dann nicht. Vielleicht wäre ein Ausbalancieren mit perfekt abgestimmten Regelanteilen möglich, jedoch fehlte die Zeit und auch das Know-how, um weitere Versuche gezielt durchführen zu können.

v = ω ∗ r

a =

v − v′
∆t

=

(ω − ω

′
) ∗ r
∆t

## Schluss

Leider ist der Balancer Robot nach aktuellen Stand (21.11.2019) noch nicht fähig, sich selbst auszubalancieren. Die Elektronik läuft, die Mechanik ist auch fertig, sodass ein erster Prototyp gebaut werden konnte. Auch die Software ermöglicht das Konfigurieren des Sensors, die Ansteuerung der Motoren und auch die Überwachung der Akkuspannung. Mithilfe des Tasters auf der Leiterplatte können der Roboter zwischen dem Balancier Modus und dem Standby Modus wechseln.

Die Nachforschungen zeigten auf, dass mithilfe eines Beschleunigungs- und Gyrosensor der Neigungswinkel des Fahrzeugs bestimmt werden kann. Auch wurde nachgewiesen, wie wichtig das saubere Aufbereiten der Daten ist. Mir wurde folgendes bewusst: „Kann man ein System nicht korrekt messen, lässt es sich auch nicht Steuern, beziehungsweise Regeln.“

Die grössten Erkenntnisse wurden überraschenderweise beim Ansteuern der Motoren gewonnen. Obwohl für die Ansteuerung der Motoren nicht viel Aufwand eingeplant wurde, brachten diese mit am meisten Schwierigkeiten. Es wurde deutlich, dass bei DC-Bürstenmotoren sehr hoher Anfahrtsstrom benötigt wird. Dadurch musste der Motortreiber gewechselt werden. Auch wurde mir bewusst, dass sich das Drehmoment der Motoren proportional zum Strom verhält. Dies führt auch direkt zum ersten Optimierungsvorschlag: Der Mikrocontroller sollte den Strom der Motoren regulieren können und nicht wie aktuell umgesetzt die Spannung über den Motoren. Dies würde eine zweite Regelung benötigen, entweder per Software oder per Hardware. So eine Regelung nennt man auch Drehmomentregler. Die neuste Version der Leiterplatte (V1.01) ermöglicht dem Mikrocontroller das Messen der Motorströme. Jedoch muss die Software mit der dazugehörigen Regelung noch implementiert werden.

Zweiter Verbesserungspunkt wäre die Motorenauswahl. Anstelle von DC-Bürstenmotoren würde ich bei nächsten Mal auf bürstenlose Motoren wechseln. Diese zahlen sich durch einen besseren Wirkungsgrad und weniger Spiel der Motorachsen aus. Bei Bürstenmotoren müssen die internen Bürsten für die Kontaktierung jedes Mal die Richtung wechseln, wenn der Motor die Drehrichtung ändert. Dies resultiert in einer grösseren Verzögerungszeit beim Richtungswechsel, sowie einer geringeren Lebensdauer der Motoren durch die mechanische Belastung der Bürsten. Jedoch sind bürstenlose Motoren komplizierter zum Ansteuern, was eine grosse Änderung der Hardware in Anspruch nehmen würde.

Sehr zufrieden bin ich mit der Software des Balancer Robots. Diese nahm auch sehr viel Zeit in Anspruch, ist dafür voll funktionstüchtig und professionell umgesetzt. Alle gewünschten Features, wie z.B. die LED-Anzeige, das Messen der Akkuspannung, das Steuern der Motoren, die Kommunikation mit dem Sensor etc. konnten umgesetzt werden.

Interessant war auch das Ausprobieren des P-Regler und PID-Regler Prinzip für den Regelungsalgorithmus. Leider reichte dies nicht für ein vollständiges Ausbalancieren. Ein Elektroingenieur mit Masterabschluss in Regelungstechnik riet mir den Einsatz eines Zustandregelers. Doch die Theorie dahinter wird erst auf dem Niveau eines Masters an der Fachhochschule behandelt.

Um meine Leitfrage zu beantworten: Ja, es ist definitiv möglich, mithilfe eines Beschleunigungs- und Gyrosensors ein Fahrzeug auf zwei Rädern auszubalancieren. Die Ergebnisse der verschieden Versuche und Experimente zeigen deutlich auf, dass der Winkel des Fahrzeugs bestimmt werden und die Motoren reguliert werden können. Mit einem geeigneten Regelungsalgorithmus müsste ein Ausbalancieren also möglich sein.

Quellenverzeichnis
Conrad: MFA 950D501 Getriebemotor https://www.conrad.ch/de/p/mfa-950d501-getriebemotor-12-v-dc-50-1-222373.html [Stand: 11.09.2019]
[Abrufdatum: 11.09.2019]

Heuler: Regelungstechnik
http://www.heuler.net/stud/pendel/html_netz/node9.html [Stand: 07.01.1997]
[Abrufdatum: 23.10.2019]

Mikrocontroller.net: Pulsweitenmodulation. https://www.mikrocontroller.net/articles/Pulsweitenmodulation [Stand: 30.09.2019]
[Abrufdatum: 30.09.2019]

NKON: Lithium-Ionen Akku
https://www.nkon.nl
[Stand: 25.10.2019]
[Abrufdatum: 25.10.2019]

Texas Instruments: L293D
http://www.ti.com/product/L293D [Stand: 24.10.2019]
[Abrufdatum: 24.10.2019]

Texas Instruments: L293D PDF http://www.ti.com/lit/ds/symlink/l293d.pdf [Stand: Januar 2016]
[Abrufdatum: 30.09.2019]

Wikipedia: Gleitender Mittelwert https://de.wikipedia.org/wiki/Gleitender_Mittelwert [Stand: 24.10.2019]
[Abrufdatum: 24.10.2019]

Wikipedia: Lithium-Ionen-Akkumulator https://de.wikipedia.org/wiki/Lithium-Ionen-Akkumulator [Stand: 14.11.2019]
[Abrufdatum: 14.11.2019]

Wikipedia: Vierquadrantensteller https://de.wikipedia.org/wiki/Vierquadrantensteller [Stand: 10.06.2017]
[Abrufdatum: 30.09.2019]

ST Microelectronics: L298 Datenblatt PDF-Datei
[Abrufdatum: 24.10.2019]

InvenSense: MPU-6050 Datenblatt. PDF-Datei
[Abrufdatum: 20.09.2019]

## Abbildungsverzeichnis

## Dank

Einen grossen Dank möchte ich an folgende Personen aussprechen:

Enrico Malancarne
Mein Elektrotechniklehrer unterstütze mich tatkräftig in der Informationsbeschaffung über Regelungstechnik. Er war meine erste Anlaufstelle, wenn Probleme in der Elektronik auftauchten, oder wenn ich Tipps brauchte für das Entwickeln des Fahrzeugs.

Hanspeter Lutz
Durch Herrn Lutz als Betreuer erfuhr ich Unterstützung, wenn es um das Verstehen der Physik des Fahrzeugs ging. Er betreute meine Klasse während der Berufsmaturitätsarbeit und gab uns einen lockeren, dennoch guten Leitfaden für das Bewältigen der BMA.

Werner Wahl
Zeitgleich zur BMA wurde ich im Geschäft im Programmieren von Embedded Software geschult. Auch wenn ich bereits vorher einige Erfahrungen im Bereich der Mikrocontrollertechnik gemacht hatte, wäre die Software des Balancer Robots nie so professionell geworden, hätte Werner mich nicht geschult und gefördert.

Christian Walser
Ohne die Einwilligung meines Lehrmeisters Christian hätte ich das ganze Projekt von Zuhause aus und auf eigene Kosten entwickeln müssen. Doch durch seine Grosszügigkeit konnte ich das Equipment der Firma für diverse Testversuche nutzen. Auch durfte ich viele Komponenten des Prototyps auf Kosten der Firma bestellen.

Aaron Scheiweiler
Meinem Lehrlingskollegen Aaron möchte ich danken für das Erstellen der 3D-Modelle und der Explosionszeichnung für die Dokumentation.

Erwin Lacher
Zuletzt möchte ich meinem Vater für das Korrekturlesen der BMA danken.

## Anhang

Schema
Balancer Robot.PDF

Software
Balancer Robot
main.h
main.c
system.c
system.h
MPU6050.h
MPU6050.c
Motors.h
Motors.c
GPIO.h
GPIO.c
I2C.h
I2C.c
LED.h
LED.c
Battery.h
Battery.c
Button.h
Button.c
Controller.h
Controller.c
DataProcessor.h
DataProcessor.c
TimingHandler.h
TimingHandler.c
ErrorHandler.h
ErrorHandler.c

Python Programm
UART Reader

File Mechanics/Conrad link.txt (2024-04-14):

https://www.conrad.ch/de/p/mfa-950d501-getriebemotor-12-v-dc-50-1-222373.html

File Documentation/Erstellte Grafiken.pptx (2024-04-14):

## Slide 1

Bildergebnis für Regelung

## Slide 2

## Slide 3

Y

Z

X

Bildergebnis für mpu6050

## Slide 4

Z

g

X

Z

g

X

α

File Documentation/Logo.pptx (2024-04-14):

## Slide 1

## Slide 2

Berufsmaturitätsschule Zürich
Berufsmaturitätsarbeit

Bildergebnis für berufsmaturitätsschule zürich logo

Technische Berufsschule Zürich
BüP 7. Semester


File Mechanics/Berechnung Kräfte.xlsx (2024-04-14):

Was | Masse [g] | Abstand zur Radachse [mm] | Drehmoment [mNm] | Winkel in Grad | Drehmoment auf der Achse | Motor Kraft | Reibungskoeffizient | Radius Reifen [mm] | Beschleunigungskraft [N] | Maximalkraft [N]
Akkuplatte | 500 | 30 | 150 | 0 | 0 | 2000 | 0.6 | 35 | 0 | 8.4
Leiterplatte | 100 | 100 | 100 | 1 | 7.330010704 | 2000 |  |  | 0.2094288772 | 8.4
Motor | 800 | -10 | -80 | 2 | 14.65778862 | 2000 |  |  | 0.4187939604 | 8.4
 |  |  | 0 | 3 | 21.98110162 | 2000 |  |  | 0.6280314749 | 8.4
 |  |  | 0 | 4 | 29.29771897 | 2000 |  |  | 0.8370776849 | 8.4
 |  |  | 0 | 5 | 36.60541195 | 2000 |  |  | 1.045868913 | 8.4
Gerüst gesamt |  |  | 250 | 6 | 43.90195457 | 2000 |  |  | 1.254341559 | 8.4
Total | 1400 |  | 420 | 7 | 51.18512423 | 2000 |  |  | 1.462432121 | 8.4
 |  |  |  | 8 | 58.4527024 | 2000 |  |  | 1.670077212 | 8.4
 |  |  |  | 9 | 65.70247532 | 2000 |  |  | 1.87721358 | 8.4
 |  |  |  | 10 | 72.93223462 | 2000 |  |  | 2.083778132 | 8.4
Motor | Drehmoment max [mNm] | Übersetzungsfaktor | Drehmoment [mNm] | 11 | 80.13977806 | 2000 |  |  | 2.289707945 | 8.4
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

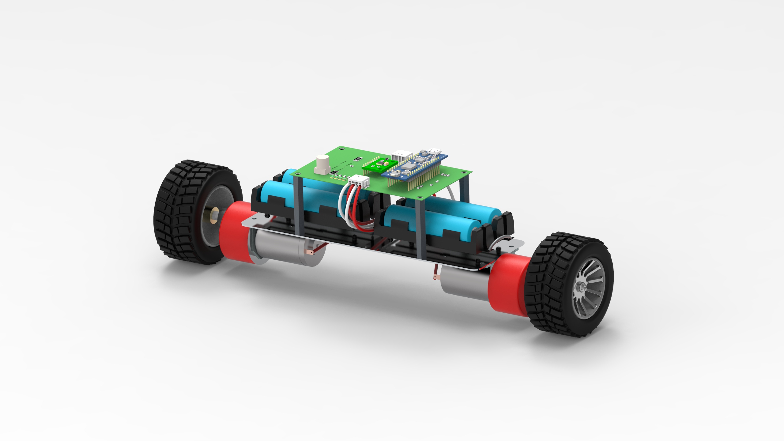
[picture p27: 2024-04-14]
Aaron Drawings/KS®2836215761.166.jpg

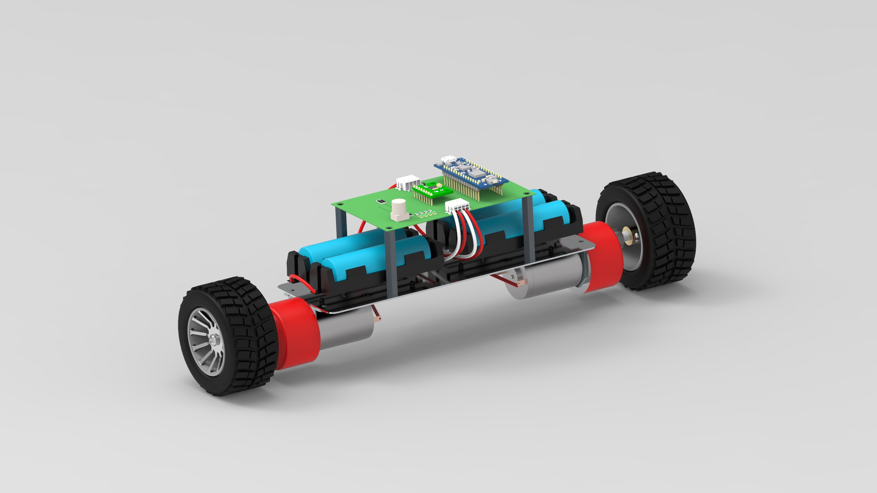
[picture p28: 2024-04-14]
Aaron Drawings/KS®2836215761.169.jpg

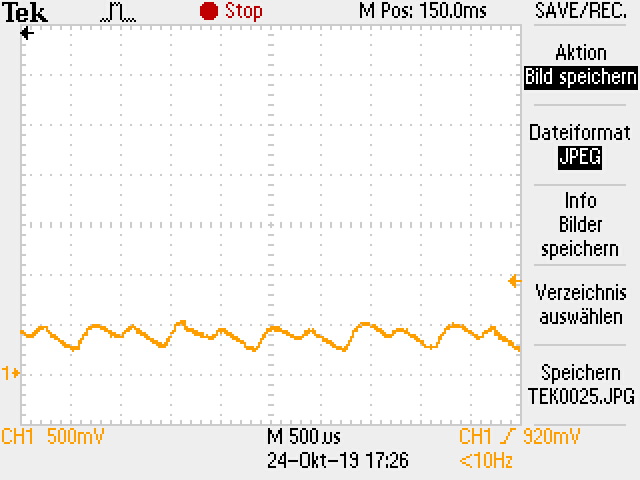
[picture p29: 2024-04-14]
Documentation/Bilder/TEK0025.JPG

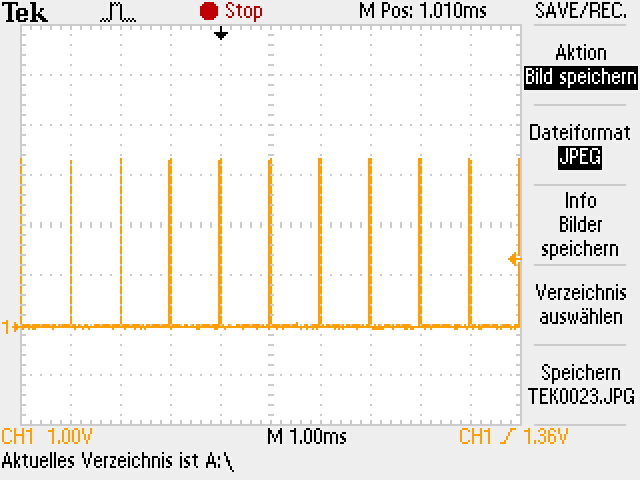
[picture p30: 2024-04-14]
Documentation/Bilder/TEK0023.JPG

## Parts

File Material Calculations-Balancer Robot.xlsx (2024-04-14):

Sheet: Kosten
Description | Supplier | Part Number | Quantity | Price | Total
Reifen | Play-Zone | P00001525 | 2 | 9.9 | 19.8
Wheel Hub | Play-Zone | P00000988 | 2 | 3.5 | 7
Motor | Conrad | 950D501 | 2 | 27.95 | 55.9
Distanzbolzen M4 40mm | Distrelec | 148-43-082 | 8 | 0.84 | 6.72
Lithium-Ionen Akkuzelle | NKON | LG INR18650-M36 3600mAh - 5A | 4 | 3.39 | 13.56
Akkuhalter | Mouser | 534-1047 | 2 | 5.01 | 10.02
Grundplatte | Eigenanfertigung | - | 1 | 5 | 5
Leiterplatte | Eigenanfertigung | - | 1 | 36.99 | 36.99
 |  |  |  |  | 154.99

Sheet: Leiterplatte
Comment | Description | Designator | Manufacturer | Part Number | Supplier 1 | Supplier Part Number 1 | Quantity | Price | Total
100n | Ceramic Capacitor 0805 | C2, C5 | Kemet | C0805C104K5RECAUT | Mouser | 80-C0805C104K5RECAUT | 2 | 0.27 | 0.54
10n | Ceramic Capacitor 0805 | C1 | Kemet | C0805C103K5RECAUT | Mouser | 80-C0805C103K5RECAUT | 1 | 0.27 | 0.27
1u | Ceramic Capacitor 0805 | C3, C6 | Kemet | C0805C105K5PACTU | Mouser | 80-C0805C105K5P | 2 | 0.32 | 0.64
100uF | Electrolyt Capacitor | C4 | Panasonic | 25SVPF100M | Mouser | 667-25SVPF100M | 1 | 1.5 | 1.5
SMD Button | SMD Button J-Lead | B1 | Würth Elektronik | 430451025836 | Mouser | 710-430451025836 (https://octopart-clicks.com/click/altium?sku=-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) | 1 | 0.49 | 0.49
Chip Resistor 10k, 0805, 1% | Resistor 10k 0.125W 0805 | R1, R2, R5, R6, R7, R8, R9, R10, R11 | Vishay | CRCW080510K0FKEAC | Mouser | 71-CRCW080510K0FKEAC (https://octopart-clicks.com/click/altium?sku=71-CRCW080510K0FKEAC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) | 9 | 0.19 | 1.71
Chip Resistor 10k, 0805, 1% | Resistor 10k 0.125W 0805 | R3, R4 | Vishay | CRCW080510K0FKEAC | Mouser | 71-CRCW080510K0FKEAC (https://octopart-clicks.com/click/altium?sku=71-CRCW080510K0FKEAC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) | 2 | 0.19 | 0.38
APT3216CGCK | LED SMD green APT3216CGCK | LED1, LED2, LED3, LED4 | Kingbright | 604-APT3216CGCK | Mouser | APT3216CGCK (https://octopart-clicks.com/click/altium?sku=APT3216CGCK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) | 4 | 0.4 | 1.6
Pin Header 4x1 2.54mm | PTSM 4 Pol | X1, X2 | Phoenix Contacdt | 1814650 | Mouser | 651-1814650 (https://octopart-clicks.com/click/altium?sku=651-1814650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) | 2 | 1.31 | 2.62
L298N | Motor Driver, 4A Output | IC2 | STMicroelectronics | L298N | Mouser | 511-L298 (https://octopart-clicks.com/click/altium?sku=511-L298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) | 1 | 4.75 | 4.75
MPU6050 | MPU6050 Sensor Board | IC1 | - | GY-521 | Digitec | 8193998 (https://octopart-clicks.com/click/altium?sku=8193998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) | 1 | 8.8 | 8.8
STM32F303K8 | Microcontroller Dev-Board | MCU1 | STMicroelectronics | NUCLEO-F303K8 | Mouser | 511-NUCLEO-F303K8 (https://octopart-clicks.com/click/altium?sku=511-NUCLEO-F303K8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) | 1 | 10.49 | 10.49
 |  |  |  |  |  |  |  |  | 33.79
Leiterplatte | Lieferant | Anzahl | Preis | Preis/stk.
Single Board Bigger V1.01 | PCBWay | 10 | 32 | 3.2
Total
36.99

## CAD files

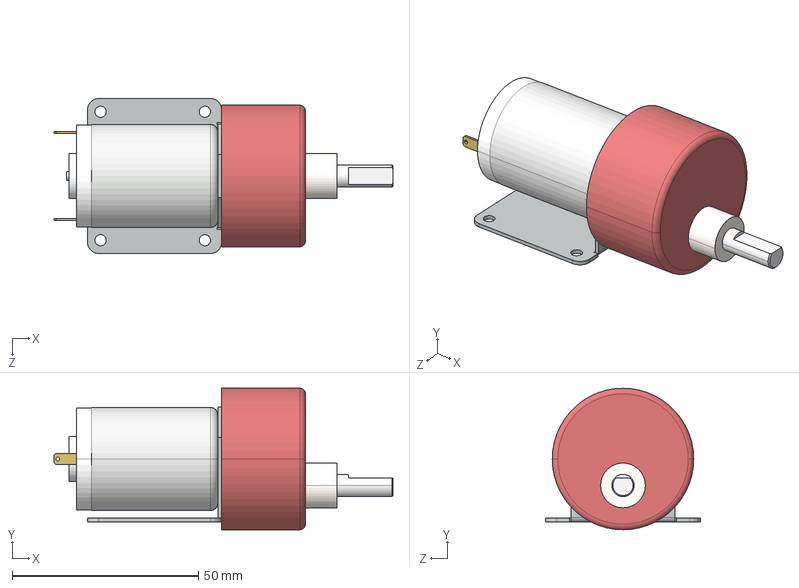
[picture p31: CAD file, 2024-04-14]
Mechanics/Documents/Motor.STEP
91.0 x 38.0 x 41.6 mm
plaque-support
moteur
reducteur
capuchon
arbre

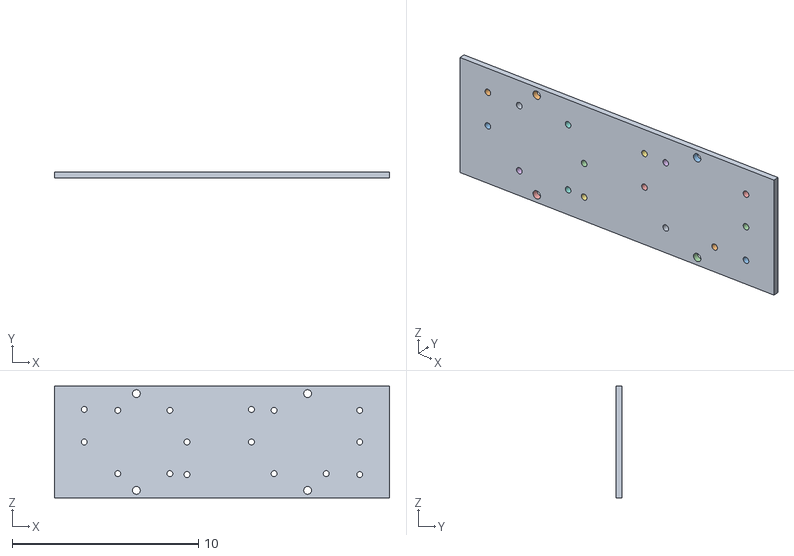
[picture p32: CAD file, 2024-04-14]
Mechanics/plate_markus_v1.0_raw (1).obj
18.0 x 0.3 x 6.00
plate
M4
M4.1
M4.2
M4.3
M3
M3.1
M3.2
M3.3
M3.4
M3.5
M3.6
M3.7
M3.8
M3.9
M3.10
M3.11
M3.12
M3.13
M3.14
M3.15

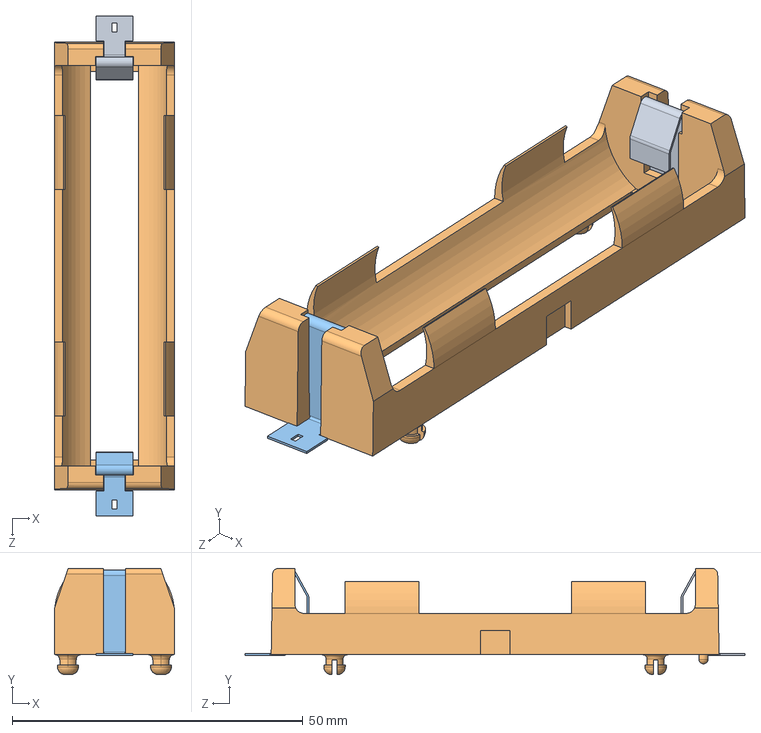
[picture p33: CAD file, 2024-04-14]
Mechanics/Documents/Batterie-Clip.STEP
20.7 x 18.3 x 86.0 mm

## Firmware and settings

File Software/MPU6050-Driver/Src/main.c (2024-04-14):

//-------------------------------------------------------------------------------
//File		:	MPU-6050.h
//Creator	:	M.Lacher
//Created	:	23.05.2018
//Function:	Header file for MPU-6050 driver
//-------------------------------------------------------------------------------

#include "main.h"
#include "MPU-6050.h"

#define ADDR 0x68

int main(void)
{
	uint16_t len = 0;
	uint8_t data[100];
	uint8_t msg[150];
	int size = 0;
	
	int16_t accelX, accelY, accelZ, gyroX, gyroY, gyroZ;
	
	initHardware();															//Initializes the nucleo board
	I2C *i2c = getDriver(); 										//Gets an I2C pointer
	MPU6050 *driver;					 									//Creates a driver pointer
	driver = initializeDevice(i2c,ADDR);				//Initializes the driver
	
	driver->setOperatingMode(STANDARD);					//Standard operating mode
	driver->gyroscope->enableAxis(X);						//Activates X-axis of gyro
	driver->gyroscope->enableAxis(Y);						//Activates Y-axis of gyro
	driver->gyroscope->enableAxis(Z);						//Activates Z-axis of gyro
	driver->accelerometer->enableAxis(X);
	driver->accelerometer->enableAxis(Y);
	driver->accelerometer->enableAxis(Z);
	
	driver->setClockSource(PLL_X_AXIS_GYRO);		//Uses the X-axis of gyro as clock source
	driver->setSampleRate(50);									//Sets sample rate to 100 samples/sec
	driver->gyroscope->setFullScaleRange(100);	//Max range gyro 1000°/s
	driver->accelerometer->setFullScaleRange(4);//Max value 4G
	driver->fifo->addToBufferList(GYROX);				//Actives fifo for gyroscope x-axis
	driver->fifo->addToBufferList(GYROY);				//Actives fifo for gyroscope y-axis
	driver->fifo->addToBufferList(GYROZ);				//Actives fifo for gyroscope z-axis
	driver->fifo->addToBufferList(ACCEL);
	driver->fifo->clearBuffer();								//Clears all data in the fifo
	driver->fifo->enable();											//Enables I2C operations on fifo   
	
  while (1)   
	{
		len = driver->fifo->getDataSize();				//Reads the datasize of the fifo
		if(len >= 12)
		{
			driver->fifo->getData(data, len);				//Reads the data of the fifo

			accelX = (data[0] << 8) + data[1];
			accelY = (data[2] << 8) + data[3];
			accelZ = (data[4] << 8) + data[5];
			gyroX = (data[6] << 8) + data[7];
			gyroY = (data[8] << 8) + data[9];
			gyroZ = (data[10] << 8) + data[11];
			
			size = snprintf(msg, sizeof(msg), "%i\t%i\t%i\t%i\t%i\t%i \r\n", accelX, accelY, accelZ, gyroX, gyroY, gyroZ);
			writeToTerminal(msg, size);
		}
	}
}
 

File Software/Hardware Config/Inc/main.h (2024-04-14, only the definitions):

#define MCO_Pin GPIO_PIN_0
#define MCO_GPIO_Port GPIOF
#define U_Batt_Pin GPIO_PIN_0
#define U_Batt_GPIO_Port GPIOA
#define ENABLE_Pin GPIO_PIN_1
#define ENABLE_GPIO_Port GPIOA
#define VCP_TX_Pin GPIO_PIN_2
#define VCP_TX_GPIO_Port GPIOA
#define PWM1_Pin GPIO_PIN_3
#define PWM1_GPIO_Port GPIOA
#define PWM2_Pin GPIO_PIN_4
#define PWM2_GPIO_Port GPIOA
#define PWM4_Pin GPIO_PIN_6
#define PWM4_GPIO_Port GPIOA
#define LED_Mode_Pin GPIO_PIN_11
#define LED_Mode_GPIO_Port GPIOA
#define LED_Error_Pin GPIO_PIN_12
#define LED_Error_GPIO_Port GPIOA
#define SWDIO_Pin GPIO_PIN_13
#define SWDIO_GPIO_Port GPIOA
#define SWCLK_Pin GPIO_PIN_14
#define SWCLK_GPIO_Port GPIOA
#define VCP_RX_Pin GPIO_PIN_15
#define VCP_RX_GPIO_Port GPIOA
#define Button_Pin GPIO_PIN_3
#define Button_GPIO_Port GPIOB
#define INT_Pin GPIO_PIN_4
#define INT_GPIO_Port GPIOB
#define INT_EXTI_IRQn EXTI4_IRQn
#define AD0_Pin GPIO_PIN_5
#define AD0_GPIO_Port GPIOB

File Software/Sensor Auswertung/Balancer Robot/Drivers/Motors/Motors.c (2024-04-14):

//------------------------------------------------------
//File:			Motors.c
//Project:	Balancer Robot
//Created:	19.09.2019
//Autor:		M.Lacher
//------------------------------------------------------

/*
This module controls the 2 motors of the Balancer Robot.
4 Pins are configured as PWM to control the motors speed.
With the function Motors_SetValue, a value between -1000 and 1000 
can be given to both motors individually.
*/

#include "Motors.h"

//PWM1 = TIM2_CH4
//PWM2 = TIM3_CH2
//PWM3 = TIM2_CH1
//PWM4 = TIM3_CH1

#define PWM1_Timer 	timer2
#define PWM2_Timer 	timer3
#define PWM3_Timer 	timer3
#define PWM4_Timer 	timer17


#define PWM1_CH			TIM_CHANNEL_4
#define PWM2_CH			TIM_CHANNEL_2
#define PWM3_CH			TIM_CHANNEL_1
#define PWM4_CH			TIM_CHANNEL_1


#define MAX_VALUE 1000
#define MIN_VALUE -1000
#define OFFSET_VALUE 0

TIM_HandleTypeDef timer2;
TIM_HandleTypeDef timer3;
TIM_HandleTypeDef timer17;

static void MX_TIM2_Init(void);
static void MX_TIM3_Init(void);
static void MX_TIM17_Init(void);

void Motors_InitModule()
{
	MX_TIM2_Init();
	MX_TIM3_Init();
	MX_TIM17_Init();
	HAL_TIM_PWM_Start(&PWM1_Timer, PWM1_CH);
	HAL_TIM_PWM_Start(&PWM2_Timer, PWM2_CH);
	HAL_TIM_PWM_Start(&PWM3_Timer, PWM3_CH);
	HAL_TIM_PWM_Start(&PWM4_Timer, PWM4_CH);
	Motors_Enable();
}

void Motors_SetValue(E_Motors motor, int16_t value)
{
	if(value > MAX_VALUE)																				//Adjust value to be in Min-Max range
	{
		value = MAX_VALUE;
	}
	else if(value < MIN_VALUE)
	{
		value = MIN_VALUE;
	}
	switch(motor)
	{
		case Motor_Left:
			if(value > 0)																						//PWM1 on, PWM2 off
			{
				__HAL_TIM_SET_COMPARE(&PWM2_Timer, PWM2_CH, 0);				//Set CCR PWM2 to 0
				__HAL_TIM_SET_COMPARE(&PWM1_Timer, PWM1_CH, value + OFFSET_VALUE);		//Set CCR PWM1 to value
			}
			else if(value < 0)																			//PWM2 on, PWM1 off
			{
				__HAL_TIM_SET_COMPARE(&PWM1_Timer, PWM1_CH, 0);				//Set CCR PWM1 to 0
				__HAL_TIM_SET_COMPARE(&PWM2_Timer, PWM2_CH, value * (-1) + OFFSET_VALUE);		//Set CCR PWM2 to value
			}
			else																										//value = 0, turn off both PWM
			{
				__HAL_TIM_SET_COMPARE(&PWM2_Timer, PWM2_CH, 0);				//Set CCR PWM2 to 0
				__HAL_TIM_SET_COMPARE(&PWM1_Timer, PWM1_CH, 0);				//Set CCR PWM1 to 0
			}
			break;
		case Motor_Right:
			if(value > 0)																						//PWM1 on, PWM2 off
			{
				__HAL_TIM_SET_COMPARE(&PWM4_Timer, PWM4_CH, 0);				//Set CCR PWM4 to 0
				__HAL_TIM_SET_COMPARE(&PWM3_Timer, PWM3_CH, value + OFFSET_VALUE);		//Set CCR PWM3 to value
			}
			else if(value < 0)																			//PWM4 on, PWM3 off
			{
				__HAL_TIM_SET_COMPARE(&PWM3_Timer, PWM3_CH, 0);				//Set CCR PWM3 to 0
				__HAL_TIM_SET_COMPARE(&PWM4_Timer, PWM4_CH, value *(-1) + OFFSET_VALUE);		//Set CCR PWM4 to value
			}
			else																										//value = 0, turn off both PWM
			{
				__HAL_TIM_SET_COMPARE(&PWM4_Timer, PWM4_CH, 0);				//Set CCR PWM4 to 0
				__HAL_TIM_SET_COMPARE(&PWM3_Timer, PWM3_CH, 0);				//Set CCR PWM3 to 0
			}
			break;
		default:
			break;
	}
}

void Motors_Enable(void)
{
	HAL_GPIO_WritePin(ENABLE_GPIO_Port, ENABLE_Pin, GPIO_PIN_SET);
}
void Motors_Disable(void)
{
	HAL_GPIO_WritePin(ENABLE_GPIO_Port, ENABLE_Pin, GPIO_PIN_RESET);
}

void MX_TIM2_Init(void)
{

  TIM_ClockConfigTypeDef sClockSourceConfig;
  TIM_MasterConfigTypeDef sMasterConfig;
  TIM_OC_InitTypeDef sConfigOC;

  timer2.Instance = TIM2;
  timer2.Init.Prescaler = 0;
  timer2.Init.CounterMode = TIM_COUNTERMODE_UP;
  timer2.Init.Period = MAX_VALUE;
  timer2.Init.ClockDivision = TIM_CLOCKDIVISION_DIV1;
  timer2.Init.AutoReloadPreload = TIM_AUTORELOAD_PRELOAD_DISABLE;
  if (HAL_TIM_Base_Init(&timer2) != HAL_OK)
  {
    _Error_Handler(__FILE__, __LINE__);
  }

  sClockSourceConfig.ClockSource = TIM_CLOCKSOURCE_INTERNAL;
  if (HAL_TIM_ConfigClockSource(&timer2, &sClockSourceConfig) != HAL_OK)
  {
    _Error_Handler(__FILE__, __LINE__);
  }

  if (HAL_TIM_PWM_Init(&timer2) != HAL_OK)
  {
    _Error_Handler(__FILE__, __LINE__);
  }

  sMasterConfig.MasterOutputTrigger = TIM_TRGO_RESET;
  sMasterConfig.MasterSlaveMode = TIM_MASTERSLAVEMODE_DISABLE;
  if (HAL_TIMEx_MasterConfigSynchronization(&timer2, &sMasterConfig) != HAL_OK)
  {
    _Error_Handler(__FILE__, __LINE__);
  }

  sConfigOC.OCMode = TIM_OCMODE_PWM1;
  sConfigOC.Pulse = 0;
  sConfigOC.OCPolarity = TIM_OCPOLARITY_HIGH;
  sConfigOC.OCFastMode = TIM_OCFAST_DISABLE;
  if (HAL_TIM_PWM_ConfigChannel(&timer2, &sConfigOC, TIM_CHANNEL_1) != HAL_OK)
  {
    _Error_Handler(__FILE__, __LINE__);
  }

  if (HAL_TIM_PWM_ConfigChannel(&timer2, &sConfigOC, TIM_CHANNEL_4) != HAL_OK)
  {
    _Error_Handler(__FILE__, __LINE__);
  }

  HAL_TIM_MspPostInit(&timer2);

}

/* TIM3 init function */
void MX_TIM3_Init(void)
{
  TIM_ClockConfigTypeDef sClockSourceConfig;
  TIM_MasterConfigTypeDef sMasterConfig;
  TIM_OC_InitTypeDef sConfigOC;

  timer3.Instance = TIM3;
  timer3.Init.Prescaler = 0;
  timer3.Init.CounterMode = TIM_COUNTERMODE_UP;
  timer3.Init.Period = MAX_VALUE;
  timer3.Init.ClockDivision = TIM_CLOCKDIVISION_DIV1;
  timer3.Init.AutoReloadPreload = TIM_AUTORELOAD_PRELOAD_DISABLE;
  if (HAL_TIM_Base_Init(&timer3) != HAL_OK)
  {
    _Error_Handler(__FILE__, __LINE__);
  }

  sClockSourceConfig.ClockSource = TIM_CLOCKSOURCE_INTERNAL;
  if (HAL_TIM_ConfigClockSource(&timer3, &sClockSourceConfig) != HAL_OK)
  {
    _Error_Handler(__FILE__, __LINE__);
  }

  if (HAL_TIM_PWM_Init(&timer3) != HAL_OK)
  {
    _Error_Handler(__FILE__, __LINE__);
  }

  sMasterConfig.MasterOutputTrigger = TIM_TRGO_RESET;
  sMasterConfig.MasterSlaveMode = TIM_MASTERSLAVEMODE_DISABLE;
  if (HAL_TIMEx_MasterConfigSynchronization(&timer3, &sMasterConfig) != HAL_OK)
  {
    _Error_Handler(__FILE__, __LINE__);
  }

  sConfigOC.OCMode = TIM_OCMODE_PWM1;
  sConfigOC.Pulse = 0;
  sConfigOC.OCPolarity = TIM_OCPOLARITY_HIGH;
  sConfigOC.OCFastMode = TIM_OCFAST_DISABLE;
  if (HAL_TIM_PWM_ConfigChannel(&timer3, &sConfigOC, TIM_CHANNEL_1) != HAL_OK)
  {
    _Error_Handler(__FILE__, __LINE__);
  }

  if (HAL_TIM_PWM_ConfigChannel(&timer3, &sConfigOC, TIM_CHANNEL_2) != HAL_OK)
  {
    _Error_Handler(__FILE__, __LINE__);
  }
  HAL_TIM_MspPostInit(&timer3);
}
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

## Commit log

2024-04-14 uploaded Documentation folder
    [Zeitplan_BMA.xlsx]
2024-04-14 uploaded Mechanics folder
    [Batterie-Clip.STEP, Berechnung Kräfte.xlsx, Motor.STEP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]
2024-04-14 uploaded div. files
    [Material Calculations-Balancer Robot.xlsx, PWM Mapping.xlsx]
2024-04-14 uploaded hardware files
    [Balancer Robot.SchDoc, Balancer Robot.PrjPcb, Balancer Robot.SchDoc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]

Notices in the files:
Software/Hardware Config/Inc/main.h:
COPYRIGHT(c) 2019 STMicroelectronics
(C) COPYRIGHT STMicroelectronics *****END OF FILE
